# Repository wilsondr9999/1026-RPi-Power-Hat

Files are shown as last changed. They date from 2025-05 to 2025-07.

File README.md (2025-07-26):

## Introduction
This project is a HAT (hardware attached on top) for the Raspberry Pi, specifically designed for the RatRig V-Core4 3D printer.  This HAT adds some features to the printer that make the electronics wiring easier and more straightforward, and prevent certain problems that can occur with the original RatRig design.

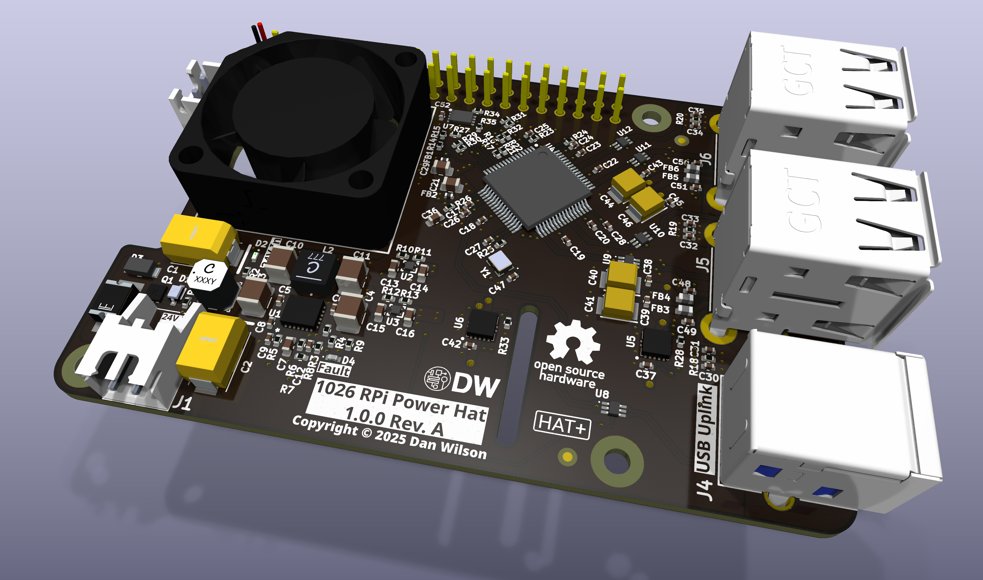
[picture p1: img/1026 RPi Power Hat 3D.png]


## Features
This HAT does the following:
- Removes the 5V power connection from the Octopus 3D printer control board that was used to power the Raspberry Pi, and replaces it with an on-board, high-current power regulator that can take 24V input directly.  This provides up to 20W (4A of 5V power) to the Raspberry Pi and all of its USB peripherals, rather than relying on the 5V regulator on the Octopus board.
- Provides an additional 4 USB ports to the Raspberry Pi using an on-board USB 2.0 hub IC.  This brings the total number of USB ports available for the 3D printer to 7 instead of 4.  The additional ports can support 2A of current each, with a total of 4A available to be shared among all 7 ports.  The USB hub IC used in this project is the Texas Instruments TUSB8041, a high-quality USB 2.0 hub.
- Includes a small fan that cools the CPU on the Raspberry Pi.  The out-of-the-box design of the V-Core4 has a large fan to cool the entire electronics enclosure, but by default it only runs when the 3D printer's stepper motors are energized.  When they are not, it does not run, and this can cause the Raspberry Pi's temperature to increase into the 60C+ range.  The on-board fan will keep the Pi below 45C when the stepper motors are not running.

## Fabrication
You can have the PCB made at any PCB manufacturer.  The Gerber files are already prepared in the Fabrication Exports folders.  One of the files is [1026 RPi Power Hat](KiCAD%20Project/Fabrication%20Exports%20-%20Oshpark/1026%20RPi%20Power%20Hat.zip) ready for upload to[ Oshpark](https://www.oshpark.com).  The other is [1026 RPi Power Hat](KiCAD%20Project/Fabrication%20Exports%20-%20PCBway/1026%20RPi%20Power%20Hat.kicad_pcb_gerber.zip) ready for upload to [PCBway](https://www.pcbway.com).  If you want to modify the design, the KiCAD project is available in the KiCAD folder.  The PCB is a 4-layer design, your PCB manufacturer needs to support a minimum trace/space of 5 mil (0.127 mm).

For assembly, the recommended method is to use solder paste and a stencil with a reflow oven or hot air station.  The stencil can be made from the [1026 RPi Power Hat-F_Paste](KiCAD%20Project/Fabrication%20Exports/1026%20RPi%20Power%20Hat-F_Paste.gbr) file in the Fabrication Exports folder.  Inexpensive stencils are available from [OshStencils](https://www.oshstencils.com/#).

## Bill of Materials (BOM)
The bill of materials to assemble this project is available in the file [1026 RPi Power Hat](KiCAD%20Project/BOM/1026%20RPi%20Power%20Hat.csv).  Almost all electronic parts are available from Mouser or Digikey.  One exception is the two inductors (L1, L2), these are probably easiest to purchase directly from CoilCraft, the link is in the BOM file.  Some miscellaneous hardware can be purchased from Amazon, those links are also in the BOM file.

## Assembly - Spreading Solder Paste for Reflow
To assemble the unit yourself, you will need a stencil and solder paste, along with a reflow oven or hot air station.  You can obtain the stencil as described above int the Fabrication section.

There is a solder stencil jig that can be 3D printed in the FreeCAD Project folder.  The file [1026 RPi Power Hat SSJ](FreeCAD%20Project/Solder%20Stencil%20Jig%20V2/1026%20RPi%20Power%20Hat%20SSJ.stl) (STL) can be imported into your preferred slicer and printed with the following settings:

- 0.2 mm layer height
- 0.4 mm nozzle
- 15% infill, use the Gyroid pattern
- PLA material

If you use PrusaSlicer, the file [1026 RPi Power Hat SSJ](FreeCAD%20Project/Solder%20Stencil%20Jig%20V2/1026%20RPi%20Power%20Hat%20SSJ.3mf) (3MF) already has these settings.  You may need to adjust the print speeds for your printer, the speeds in the 3MF file are set for a RatRig V-Minion and are quite fast.

If you want to change aspects of the Solder Stencil Jig, the FreeCAD file is available named [Solder Stencil Jig V2](FreeCAD%20Project/Solder%20Stencil%20Jig%20V2/Solder%20Stencil%20Jig%20V2.FCStd), it is a parametric file that can generate a solder stencil jig for any PCB.

Once you have obtained the manufactured PCB, the stencil, and have printed the solder stencil jig, you should have all 3 of them as such:

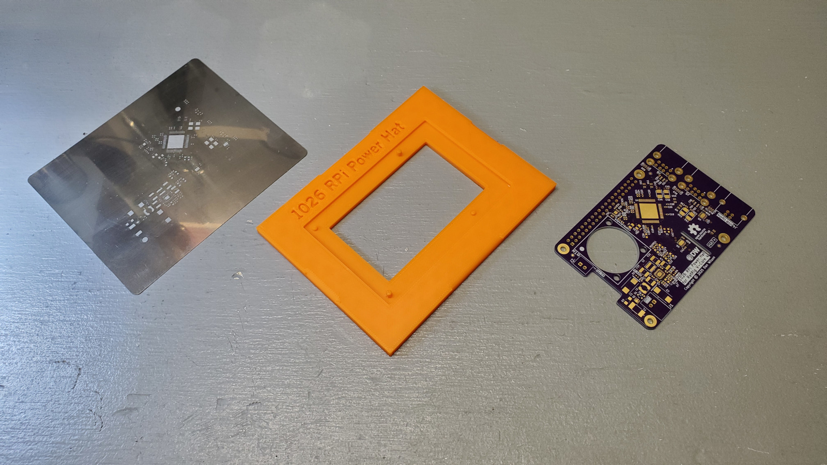
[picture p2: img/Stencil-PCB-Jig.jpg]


Insert the PCB into the solder stencil jig, the registration pins will go through the mounting holes:

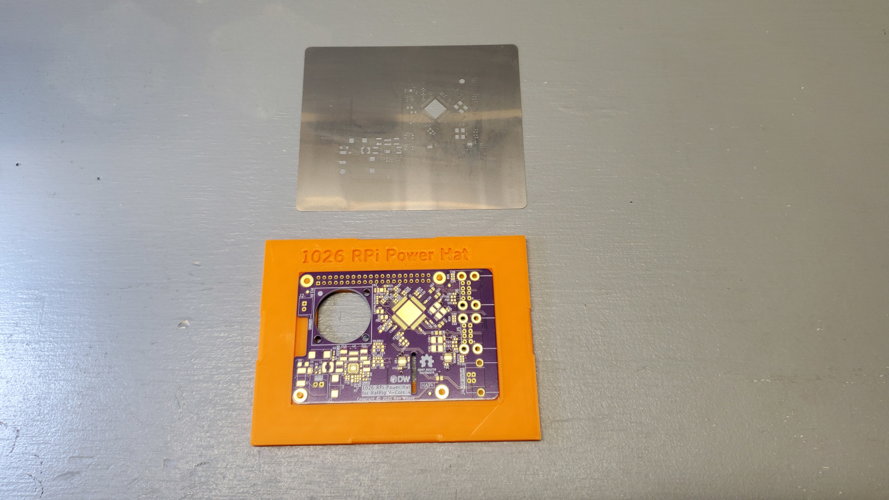
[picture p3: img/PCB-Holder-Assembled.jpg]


Clean the PCB surface with isopropyl alcohol (99%), and clean the stencil the same way.  The PCB should look completely clean under a microscope, with no dust, hair, fibers, or oils on the PCB:

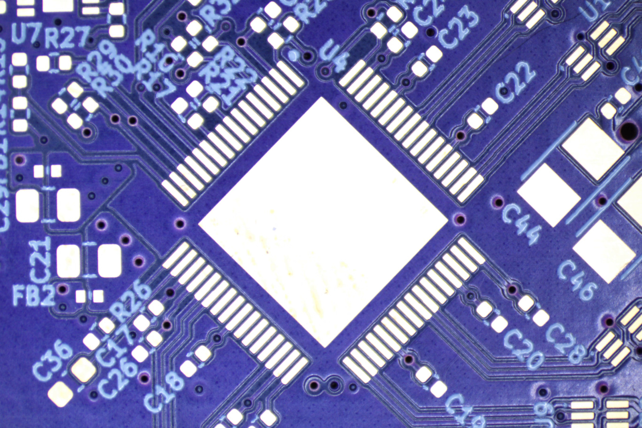
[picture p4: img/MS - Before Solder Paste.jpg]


Finally, place the stencil on top of the jig, two of the registration pins go through the stencil to align it:

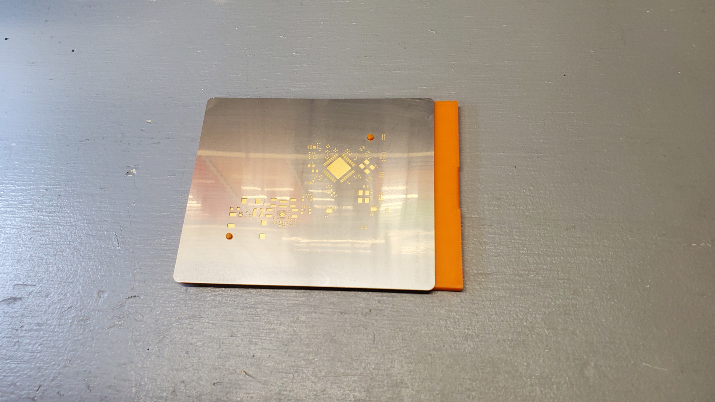
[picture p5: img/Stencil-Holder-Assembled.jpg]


Spread the solder paste onto the stencil using a paste spreader or old plastic card.  Ensure the solder paste fills all openings in the stencil.  Remove the stencil, then carefully pop out the PCB from the jig.  **Do NOT leave the PCB in the jig while placing the components in the next step!**  The components will dislodge from the PCB when you pop it out later.

Your PCB pads should look like this after solder paste is applied:

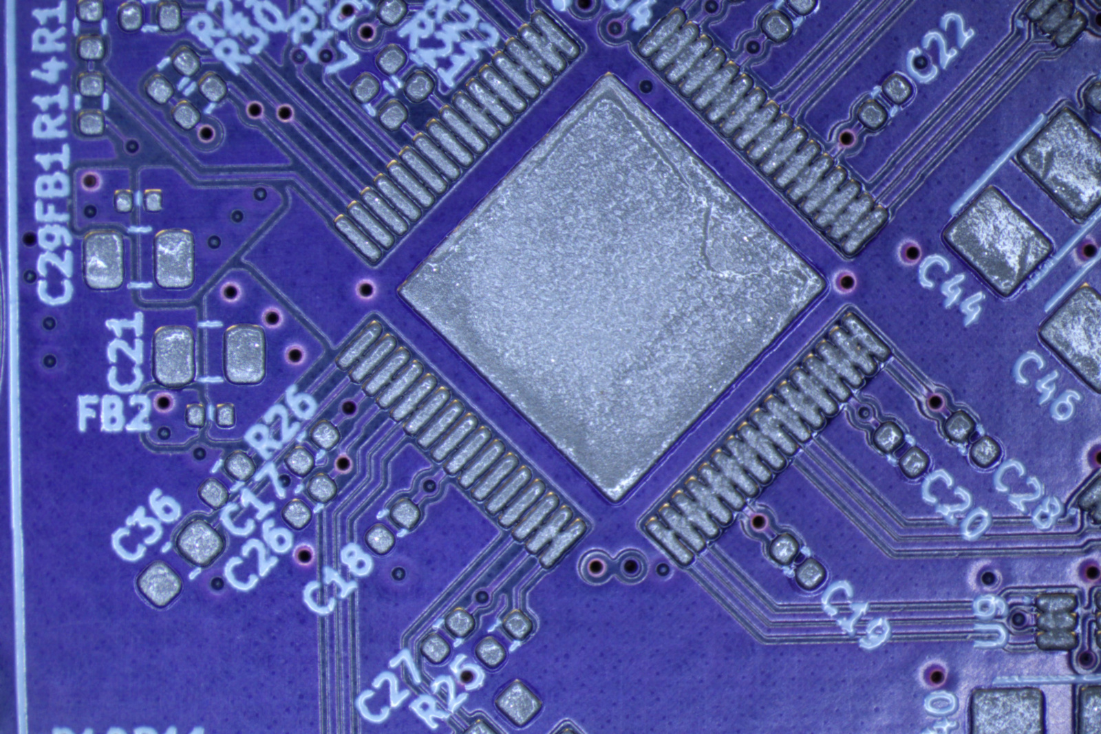
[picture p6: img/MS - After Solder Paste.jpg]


## Assembly - Placing Components
Begin placing the surface mount components onto the PCB.  Start with the smallest components (0402 surface mount passives -- resistors, capacitors), and work up to the larger components.  Do not place any through-hole components at this stage.  You can place the components with tweezers or use an air-pick tool if available.

You do not need to perfectly align every component, if the component leads are touching the solder paste on the correct pads and the component is flat, you're fine.  When the board is reflowed, the surface tension of the solder paste will pull the components into very good alignment with the pads.

If the solder paste has expanded and is touching adjacent pads like on the USB chip, it probably will not cause an issue.  When the solder melts, the flux and the solder mask on the PCB will direct the liquid solder to the pad and separate the adjacent pins.  After reflow, check carefully for any solder bridges that may remain.

Double- and Triple- check the polarity of the diodes, LEDs, and capacitors when you place them on the PCB, and check the pin 1 marker of all of the chips.  The silkscreen markings on the PCB match the mark on the component (provided you are using the exact component listed in the BOM).

The 0402 LEDs in particular are very difficult to identify which end is the cathode, so carefully check.

Unlike aluminum electrolytic capacitors where the negative terminal is marked, the tantalum polymer capacitors you will be soldering here have the positive terminal marked.  This matches the silkscreen on the PCB.

Once you get to the larger components, you need to carefully look at the pin alignment, especially on the big USB chip.  It is very easy to misalign the chip by one pin in any direction, so double-check it.

Your PCB should look like this after the components are placed:

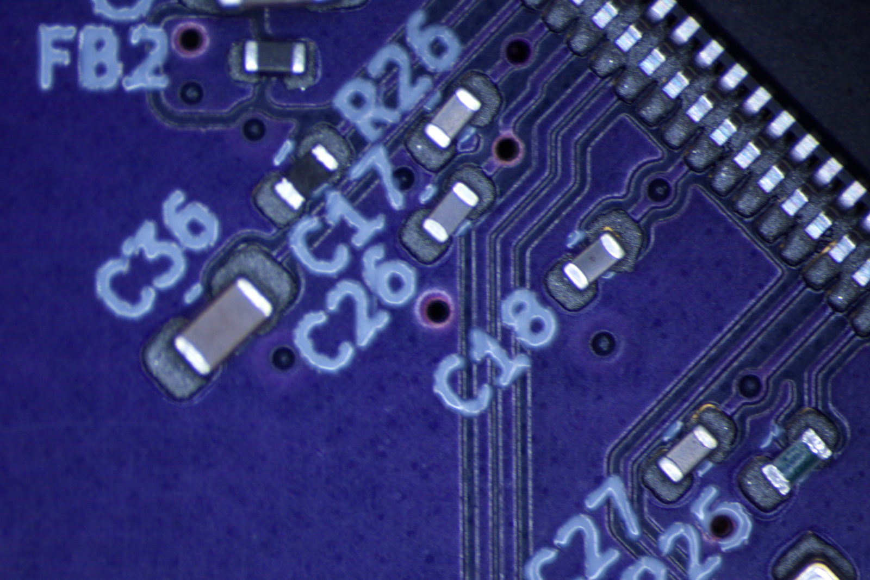
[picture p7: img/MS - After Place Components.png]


## Assembly - Reflow
Reflow the PCB in a reflow oven using the solder paste manufacturer's recommended reflow profile.

If you are going to reflow with a hot air station, you need to be extremely careful with the heat level, as some components like the LEDs can melt if the temperature is too high.  Furthermore, the air flow needs to be low, as some of the very small 0402 components can be blown off the PCB.  If you have a PCB preheater, it will be very helpful here.

## Assembly - Through-Hole Components
Solder the through-hole components onto the PCB in the following order:
The following components are on the TOP side of the PCB, so we solder them on from the back side (bottom):
- 2x JST-XH-2 connectors for input power and the fan.  The fan connector is a top-entry, the input power connector is a side-entry.
- 1x USB-B connector for uplink
- 2x USB-A (2 port) connectors for downlink

The following component is on the BOTTOM side of the PCB, so we solder it on from the front side (top):
- 2x20 pin header

Look at the silkscreen marks on the PCB, they identify the side where the component goes.  Then you solder from the other side.

## Cleaning
It is recommended to clean the PCB after soldering to remove all remaining flux.  Isopropyl alcohol will remove it, but may require light brushing with a toothbrush, and may require multiple passes to remove all of the flux.  Use only distilled water or isopropyl alcohol as solvents for cleaning the PCB.  An ultrasonic cleaner with a detergent also works well if available, but **never use Isopropyl alcohol in an ultrasonic cleaner, use distilled water and detergent only.**

If you have used distilled water for rinsing or in an ultrasonic cleaner, dry the PCB using compressed air, and then further dry it in an oven at 125C for 2 hours.

Once you're finished, your PCB should look like this:

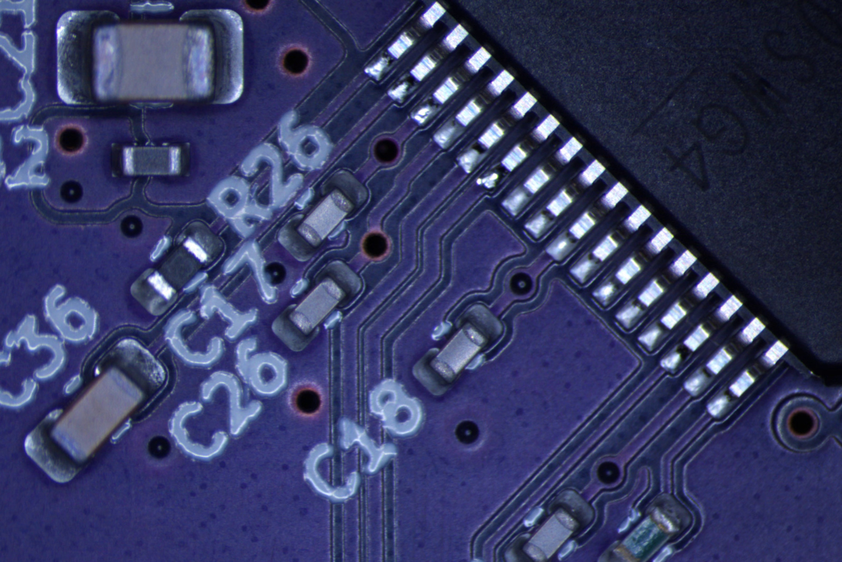
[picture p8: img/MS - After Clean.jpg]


## Fan Preparation
The fan that is to be installed on the PCB needs to have the JST-XH-2 connector (part number XHP-2) installed.  Cut the wires on the fan to a length of approximately 2 inches (5 cm), then crimp on two of the JST contacts (part number SXH-001T-P0.6).  Insert the crimped wire/contacts into the XHP-2 connector, pay attention to the required polarity.  The polarity is marked on the PCB, the fan's red wire goes to the positive (+) terminal on the PCB, this is the terminal closest to the M2.5 mounting screw hole.

Use the following picture as a reference for the fan wiring:

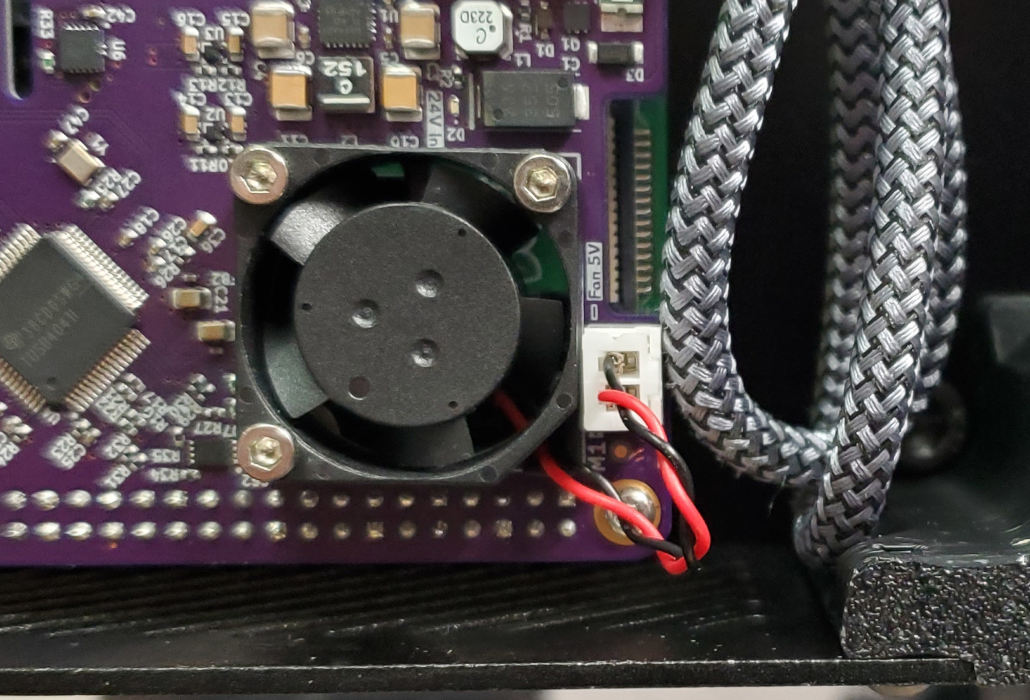
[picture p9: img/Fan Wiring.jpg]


Once the fan is terminated, attach it to the PCB using 3x M2.5 16mm hex cap screws and 3 M2.5 hex nuts on the underside of the PCB.  Ensure the fan is oriented correctly such that the air flow is from the top of the PCB through to the bottom of the PCB.  This will blow air onto the Raspberry Pi's CPU that is below.  For maximum effectiveness, add a passive heat sink to the Raspberry Pi's CPU chip.  There are two arrows on the side of the fan that show you both the rotation direction as well as the air flow direction, you can use these to assist you in orienting the fan in the correct position.

## 5V Regulator Heat Sink
There is a square on the bottom side of the PCB that is 6mm x 6mm in size that is bare copper, not covered by solder mask.  This square is directly underneath the 5V regulator and needs to have a small copper heat sink attached to make sure the regulator stays cool.  The heat sink is listed in the BOM .csv file, and is available from Amazon.  Peel off the protective film on the heat sink and press it to the copper square so that it sticks on.  The fan's air flow will also help cool this heat sink.

## Installation into the RatRig V-Core 4
Prepare a 2-wire power lead to go from the 24V power supply in the V-Core4 to the power HAT.  Terminate the ends of the lead on the 24V power supply side using connectors applicable to your power supply.

Terminate the HAT ends of the leads using a JST-XH-2 connector (part number XHP-2) the same way you did the fan.  Crimp on two of the JST contacts (part number SXH-001T-P0.6).  Insert the crimped wire/contacts into the XHP-2 connector, pay attention to the required polarity.  The polarity is marked on the PCB, the negative lead is on the side of the PCB's JST-XH-2 connector that is closest to the M2.5 mounting screw hole.

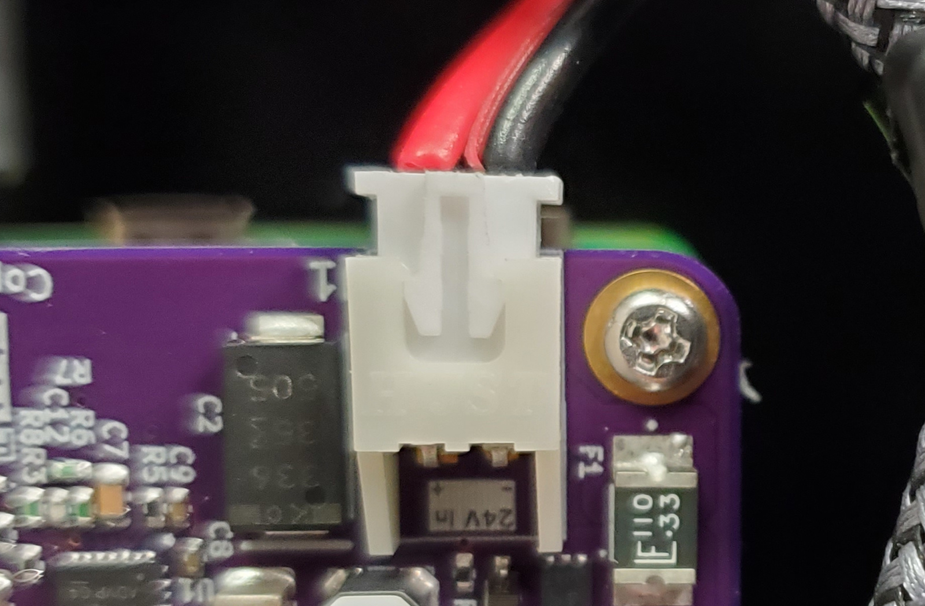
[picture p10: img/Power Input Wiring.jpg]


You will be assembling the HAT onto the top of your Raspberry Pi using 4 brass PCB standoffs (20mm length of the standoff + a 6 mm length of M2.5 threads) and 4 M2.5 x 6mm screws (pan-head phillips).  The BOM .csv file has an Amazon link to a kit that contains these parts.  Use the following photo to see how the HAT is supposed to be mounted on top of the Raspberry Pi:

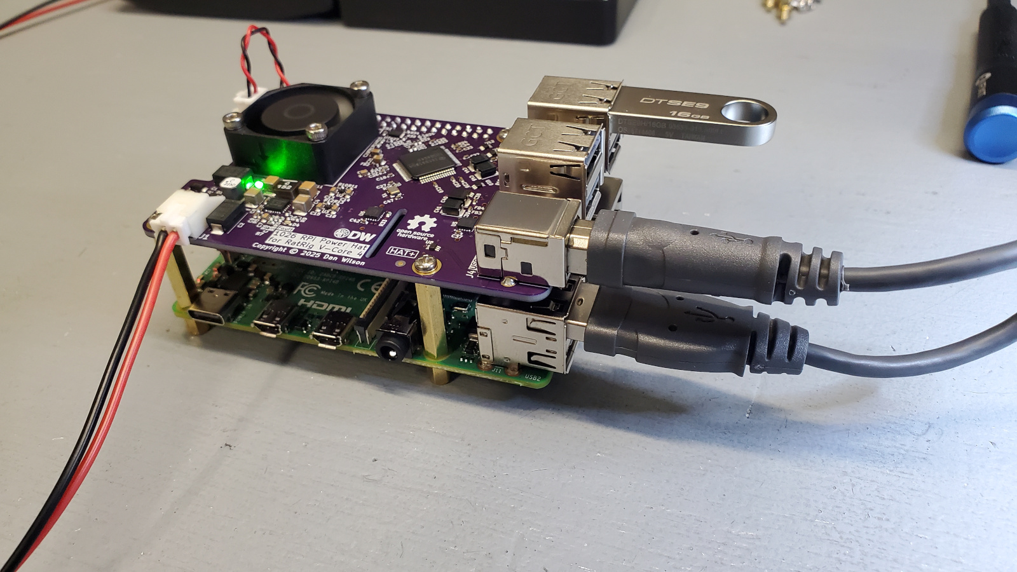
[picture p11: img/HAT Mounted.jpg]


Mount the HAT to the Raspberry Pi inside the V-Core4's electronics case.  The final result should look like this:

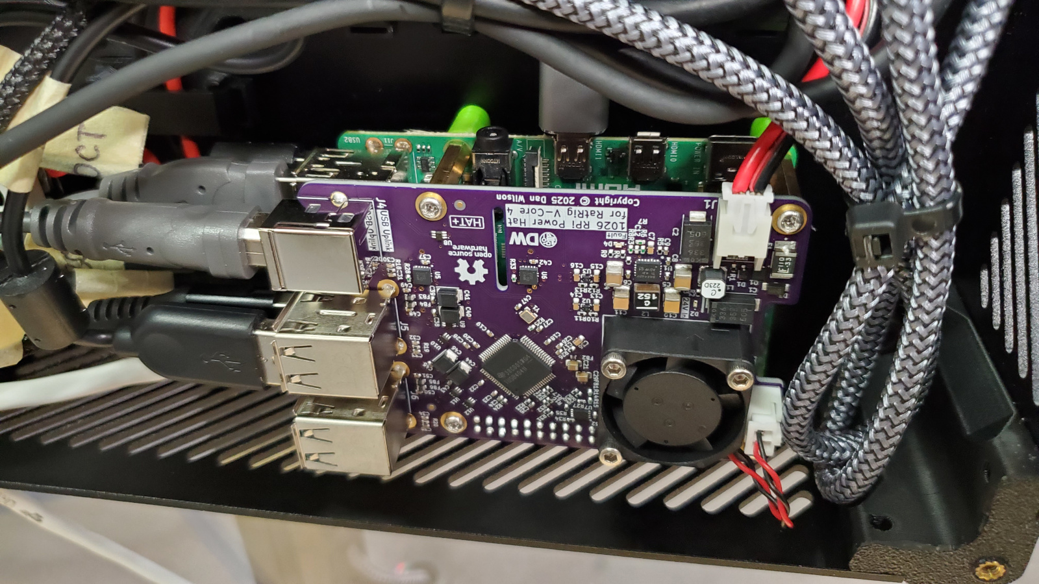
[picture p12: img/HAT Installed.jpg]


## USB Port Recommendations
Some of the USB devices on the RatRig V-Core4 have higher bandwidth requirements, and/or are more sensitive to issues than others.  Please use the following recommendations for which devices to plug where:

For all V-Core 4 models:
- Plug the USB-A to USB-B cable that connects the Raspberry Pi to the HAT using:
	- 1 USB-A 2.0 port on the Raspberry Pi (black plastic)
	- The USB-B port on the HAT

For CoreXY and Hybrid models:
- Toolhead / EBB42 board: Use a Raspberry Pi 3.0 (blue plastic) port
- Beacon Probe: Use a Raspberry Pi 3.0 (blue plastic) port
- Octopus Board: Use a Raspberry Pi 2.0 (black plastic) port
- Additional accessories, such as a chamber camera, nozzle camera, or touchscreen: Use a USB 2.0 port (black plastic) on the HAT

For IDEX models:
- Toolhead / EBB42 board 0: Use a Raspberry Pi 3.0 (blue plastic) port
- Toolhead / EBB42 board 1: Use the other Raspberry Pi 3.0 (blue plastic) port
- Beacon Probe: Use a Raspberry Pi 2.0 (black plastic) port
- Octopus Board: Use a USB 2.0 (black plastic) port on the HAT
- VAOC Offset Camera: Use a USB 2.0 (black plastic) port on the HAT
- Additional accessories, such as a chamber camera, nozzle camera, or touchscreen: Use a USB 2.0 port (black plastic) on the HAT

Your final installation should look like this:

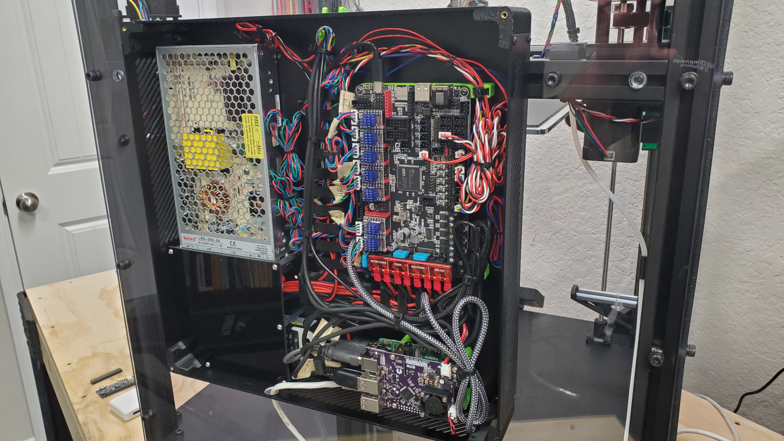
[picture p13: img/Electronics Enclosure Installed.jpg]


## Initial Power-Up
At this point, if everything is connected, you can power on the V-Core4.  The HAT will provide the 5V power to the Pi through the GPIO header.  You should see the green power-on LED lit on the HAT.  If you see the red Fault LED lit up on the HAT, check your input voltage, it must be above 22V for the HAT to power on.  If the voltage checks out OK but you still get a fault LED, this may indicate that you have a short on the HAT PCB.  Re-check all soldered connections.

The fault LED can also indicate an overcurrent condition (more than 20W / 4A used by the Pi + fan + all USB devices).  This should be unlikely, but is something to check.  Remove USB devices one at a time, starting with the accessories that are not part of the RatRig V-Core4 systems and see if the fault light goes out.

## Preparing the HAT in Linux
This HAT conforms to the Raspberry Pi HAT+ specification.  The HAT+ specification requires that the HAT contain an EEPROM with information that tells the Raspberry Pi what the HAT is and its capabilities.  We will program this EEPROM and set up the Raspberry PI to recognize it in the next steps.

### Establish a Command Session to your Raspberry Pi
Using an SSH client like [Putty](https://www.putty.org/), connect to your Raspberry Pi using it's IP address on port 22.  The default username and password for the Raspberry Pi, if you have prepared it using RatRig's instructions, is "pi" and "raspberry".  If you have changed these, use your own username and password that you have established.

Once in the command terminal, execute the following commands to prepare the EEPROM:

```
sudo -i
```

The above command will again ask you for the password, the default is "raspberry".

```
apt install cmake
cd /root
git clone https://github.com/raspberrypi/utils.git
cd utils/eeptools
cmake .
make
make install
wget https://github.com/wilsondr9999/1026-RPi-Power-Hat/blob/master/Extras/Linux%20EEPROM%20Preparation/myhat.eep
wget https://github.com/wilsondr9999/1026-RPi-Power-Hat/blob/master/Extras/Linux%20EEPROM%20Preparation/rr-vcore4-powerhat.dtbo
apt install i2c-tools
dtoverlay i2c-gpio i2c_gpio_sda=0 i2c_gpio_scl=1 bus=9
i2cdetect -y 9
```

 The final command above should show you a matrix of detected I2C addresses on the GPIO header.  The HAT is supposed to be detected on address 53, and the number 53 should show up in the matrix.  If it does not, check the HAT for soldering problems.  If it does, proceed with flashing the EEPROM:

```
./eepflash.sh -w -t=24c32 -d=9 -a=53 -f=myhat.eep
```

Make sure the above command completes successfully and does not issue an error message.

```
cp rr-vcore4-powerhat.dtbo /boot/overlays/
sh -c "echo rr-vcore4-powerhat.dtbo >> /boot/config.txt"
```

Now we can reboot the Pi:

```
reboot
```

Once the Pi is rebooted, you can verify that the USB hub is detected and functioning.  Connect to a command session again using your SSH client, and issue the following command:

```
lsusb
```

In the device listing, you should see the HAT's USB hub:

```
Bus 001 Device 005: ID 0451:8142 Texas Instruments, Inc. TUSB8041 4-Port Hub
```

You should also be able to see the RatRig printer devices connected:

```
Bus 001 Device 006: ID 1d50:614e OpenMoko, Inc. stm32f446xx
Bus 001 Device 004: ID 04d8:e72b Microchip Technology, Inc. Beacon RevH
Bus 001 Device 003: ID 1d50:614e OpenMoko, Inc. stm32g0b1xx
Bus 001 Device 002: ID 2109:3431 VIA Labs, Inc. Hub
```

You should also see any additional accessory devices you have added, for example:

```
Bus 001 Device 008: ID 04d9:8030 Holtek Semiconductor, Inc. BTT-HDMI7
Bus 001 Device 007: ID 046d:0825 Logitech, Inc. Webcam C270
```

## Licensing
This project is licensed under two separate licenses:

The hardware design is licensed under the CERN Open Hardware License Version 2 - Weakly Reciprocal.  This copyleft license requires that if you use this device in your product or redistribute this device or its derivatives in any way, that you must:

- Provide the end-users with this license and copyright notice.
- State any changes you have made to the original device, its files, or its documentation.
- Publish your modifications of the device, its files, and its documentation under the same license.
- Indicate to the end-user the original source (this GitHub archive) and that your work is a derivative and/or redistribution.
- The license is "weakly reciprocal" in that it only requires these actions for the modified device itself, not the entire end product that you have incorporated it into.  The rest of the product does not have to follow this license and is not affected by this license.

The documentation, images, and instructions are licensed under the Creative Commons Attribution-ShareAlike 4.0 International Public License.  This copyleft license requires that if you use this device in your product or redistribute this device or its derivatives in any way, that you must:

- Provide the end-users with this license and copyright notice.
- State any changes you have made to the original device, its files, or its documentation.
- Publish your modifications of the device, its files, and its documentation under the same license.
- Indicate to the end-user the original source (this GitHub archive) and that your work is a derivative and/or redistribution.

As stated by the licenses, all uses of this project require attribution and require open-source release under the same licenses.

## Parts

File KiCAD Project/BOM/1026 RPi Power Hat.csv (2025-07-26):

Reference | Qty | Value | DNP | Exclude from BOM | Footprint | Datasheet | Height | Manufacturer_Name | Manufacturer_Part_Number | Mouser Part Number | Product Page | Spec | Description
C1,C2 | 2 | T521D336M035ATE065 |  |  | DW_Passives:[C] Kemet Tantalum Polymer T521X | https://www.mouser.com/datasheet/2/447/KEM_T2076_T52X_530-3317002.pdf | 4.3 | KEMET | T521D336M035ATE065 | 80-T521D336M35ATE65 | https://www.mouser.com/ProductDetail/KEMET/T521D336M035ATE065?qs=1gHfTFoodzaHxXmfIl2UDw%3D%3D | 33u 35V | Input Filter Cap Tant Poly
C3,C4 | 2 | GRJ32ER71H106KE11K |  |  | Capacitor_SMD:C_1210_3225Metric | https://www.mouser.com/datasheet/2/281/1/GRJ32ER71H106KE11_02A-3155002.pdf | 2.8 | Murata | GRJ32ER71H106KE11K | 81-GRJ32ER71H106KE1K | https://www.mouser.com/ProductDetail/Murata-Electronics/GRJ32ER71H106KE11K?qs=lEfY3O89Aqkc0aIiWmlJZw%3D%3D | 10u 50V | Input Capacitor
C5,C6 | 2 | GCM155R71H223KA55D |  |  | Capacitor_SMD:C_0402_1005Metric | https://www.mouser.com/datasheet/2/281/1/GCM155R71H223KA55_01A-3142318.pdf | 0.55 | Murata | GCM155R71H223KA55D | 81-GCM155R71H223KA5D | https://www.mouser.com/ProductDetail/Murata-Electronics/GCM155R71H223KA55D?qs=aEuGZpxfbxWRPp0xzcGE2w%3D%3D | 22n 50V | Input Capacitor
C7,C13,C14,C15,C16,C36 | 6 | GCM188R71C105KA64J |  |  | Capacitor_SMD:C_0603_1608Metric | https://www.mouser.com/datasheet/2/281/1/GCM188R71C105KA64_04A-3143889.pdf | 0.9 | Murata | GCM188R71C105KA64J | 81-GCM188R71C105KA4J | https://www.mouser.com/ProductDetail/Murata-Electronics/GCM188R71C105KA64J?qs=4%252BGqC78dy0BN5WaW5TLgXw%3D%3D | 1u 16V | Vcc Capacitor
C8,C9,C17,C18,C19,C20,C22,C23,C24,C25,C26,C27,C28,C37,C38,C39,C42,C43,C45,C47,C48,C49,C50,C51,C52 | 25 | GCM155R71C104KA55D |  |  | Capacitor_SMD:C_0402_1005Metric | https://www.mouser.com/datasheet/2/281/1/GCM155R71C104KA55_01A-3142292.pdf | 0.55 | Murata | GCM155R71C104KA55D | 81-GCM155R71C104KA5D | https://www.mouser.com/ProductDetail/Murata-Electronics/GCM155R71C104KA55D?qs=aEuGZpxfbxVTPYRtXT4ecg%3D%3D | 100n 16V | Cboot Capacitor
C10,C11 | 2 | GCM32ER71C226ME19L |  |  | Capacitor_SMD:C_1210_3225Metric | https://www.mouser.com/datasheet/2/281/1/GCM32ER71C226ME19_01A-3146418.pdf | 2.7 | Murata | GCM32ER71C226ME19L | 81-GCM32ER71C226ME9L | https://www.mouser.com/ProductDetail/Murata-Electronics/GCM32ER71C226ME19L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 | 22u 16V | Output Capacitor
C12 | 1 | VJ0402A100GXJCW1BC |  |  | Capacitor_SMD:C_0402_1005Metric | https://www.vishay.com/doc?28548 | 0.5 | Vishay | VJ0402A100GXJCW1BC | 77-VJ0402A100GXJCBC | https://www.mouser.com/ProductDetail/77-VJ0402A100GXJCBC | 10p 16V C0G | Cff Capacitor
C21,C29 | 2 | GCM21BR70J106KE22K |  |  | Capacitor_SMD:C_0805_2012Metric | https://www.mouser.com/datasheet/2/281/1/GCM21BR70J106KE22_01A-3145361.pdf | 1.4 | Murata | GCM21BR70J106KE22K | 81-GCM21BR70J106KE2K | https://www.mouser.com/ProductDetail/Murata-Electronics/GCM21BR70J106KE22K | 10u 6V3 | 3V3 Bus Capacitor
C30,C33,C35 | 3 | GCM155R71H104KE02J |  |  | Capacitor_SMD:C_0402_1005Metric | https://www.mouser.com/datasheet/2/281/1/GCM155R71H104KE02_01A-3142168.pdf | 0.55 | Murata | GCM155R71H104KE02J | 81-GCM155R71H104KE2J | https://www.mouser.com/ProductDetail/Murata-Electronics/GCM155R71C104KA55D?qs=aEuGZpxfbxVTPYRtXT4ecg%3D%3D | 100n 50V | USB Shield EMI Cap
C31,C32,C34 | 3 | GCM155R71H102KA37D |  |  | Capacitor_SMD:C_0402_1005Metric | https://www.mouser.com/datasheet/2/281/1/GCM155R71H102KA37_01A-3142409.pdf | 0.55 | Murata | GCM155R71H102KA37D | 81-GCM155R71H102KA7D | https://www.mouser.com/ProductDetail/Murata-Electronics/GCM155R71H102KA37D | 1n 50V | USB Shield EMI Cap
C40,C41,C44,C46 | 4 | TCJB157M006R0070 |  |  | DW_Passives:[C] Kyocera AVC Tant Poly TCJB157M006R0070 | https://www.mouser.com/datasheet/2/40/TCJ-2887130.pdf | 2.1 | Kyocera AVX | TCJB157M006R0070 | 581-TCJB157M006R0070 | https://www.mouser.com/ProductDetail/KYOCERA-AVX/TCJB157M006R0070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 | 150u 6V3 | AVX 150uF SMD Solid Polymer Tantalum Electrolytic Capacitor, 6.3 V dc +/-20%, TCJ Series
D1 | 1 | PDZ10B,115 |  |  | DW_Semiconductors:[D] Nexperia Zener PDZ10B,115 10V | https://www.mouser.com/datasheet/2/916/PDZ_B_SER-1548405.pdf | 1.1 | Nexperia | PDZ10B,115 | 771-PDZ10B115 | https://www.mouser.com/ProductDetail/Nexperia/PDZ10B115?qs=LOCUfHb8d9t6BsAtogB8tA%3D%3D | 10V 2% 400mW | Rev Power Prot Diode
D2 | 1 | 150040GS73220 |  |  | DW_Optoelectronics:[D] Wurth Elektronik 150040GS73220 | https://www.we-online.com/components/products/datasheet/150040GS73220.pdf | 0.35 | Wurth Elektronik | 150040GS73220 | 710-150040GS73220 | https://www.mouser.com/ProductDetail/Wurth-Elektronik/150040GS73220?qs=u16ybLDytRZ9vktXLUK1Kg%3D%3D | 0603 525nm | Input Power LED
D3 | 1 | SMF24CA |  |  | DW_CircuitProtection:[D] Littelfuse SMF24CA 24V 200W | https://www.mouser.com/datasheet/2/240/media-3321418.pdf | 1.08 | Littelfuse | SMF24CA | 576-SMF24CA | https://www.mouser.com/ProductDetail/Littelfuse/SMF24CA?qs=d0WKAl%252BL4KZ7Y3Ls3uQ%252BqA%3D%3D | TVS BiDir 24V 200W | Input TVS Surge Suppression
D4 | 1 | 150040RS73240 |  |  | DW_Optoelectronics:[D] Wurth Elektronik 150040RS73240 | https://katalog.we-online.de/pbs/datasheet/150040RS73240.pdf | 0.5 | Wurth Elektronik | 150040RS73240 | 710-150040RS73240 | https://www.mouser.co.uk/ProductDetail/Wurth-Elektronik/150040RS73240?qs=8Aam6%252B7C6HGMiInmnlrBiw%3D%3D | 0402 630nm | Fault LED
F1 | 1 | 1812L110/33MR |  |  | DW_CircuitProtection:[F] Littelfuse PPTC 1812L110/33MR | https://www.littelfuse.com/assetdocs/resettable-ptcs-1812l-datasheet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 | 1.25 | LITTELFUSE | 1812L110/33MR | 576-1812L110/33MR | https://www.mouser.com/ProductDetail/Littelfuse/1812L110-33MR?qs=PWhpLWeW8wdL8%252Bas2HFkoA%3D%3D | 1.1A 33V | Input PPTC Resettable Fuse
FB1,FB2 | 2 | BLM15PX221SZ1D |  |  | DW_Passives:[FB] Murata BLM15PX221SZ1D | https://www.mouser.com/datasheet/2/281/QNFA9118-1915745.pdf | 0.55 | Murata Electronics | BLM15PX221SZ1D | 81-BLM15PX221SZ1D | https://www.mouser.com/ProductDetail/Murata-Electronics/BLM15PX221SZ1D | 220 ohm 100MHz | BLM15_Z1D Series EMI Suppression Filter 220+/-25% at 100MHz 1.4A @85
FB3,FB4,FB5,FB6 | 4 | BLM18KG221SN1D |  |  | DW_Passives:[FB] Murata BLM18KG221SN1D 220ohm 2.2A | https://www.mouser.com/datasheet/2/281/ENFA0003-1915778.pdf | 0.55 | Murata Electronics | BLM18KG221SN1D | 81-BLM18KG221SN1D | https://www.mouser.com/ProductDetail/Murata-Electronics/BLM18KG221SN1D | 220ohm 2.2A | BLM18 Series EMI Suppression Filter 220+/-25% at 100MHz 2.2A @85
J1 | 1 | S2B-XH-A-1 |  |  | DW_Connectors:[J] JST S2B-XH-A-1 | https://www.jst-mfg.com/product/pdf/eng/eXH.pdf | 7 mm | JST | S2B-XH-A-1 | 306-S2BXHA1LFSN | https://www.mouser.com/ProductDetail/JST-Commercial/S2B-XH-A-1LFSN?qs=QpmGXVUTftHhNeC%252BPQWeTw%3D%3D | JST-XH-2 Side | Input Power Connector
J2 | 1 | B2B-XH-A(LF)(SN) |  |  | DW_Connectors:JST_B2B-XH-A(LF)(SN) | https://www.jst-mfg.com/product/pdf/eng/eXH.pdf | 7 mm | JST | B2B-XH-A(LF)(SN) | 306-B2BXHALFSNP | https://www.mouser.com/ProductDetail/JST-Commercial/B2B-XH-ALFSN?qs=cdbOS8ANM9DdcSn9qRmfCw%3D%3D | JST-XH-2 | Connector Header Through Hole 2 position 0.098 (2.50mm)
J3 | 1 | ESW-120-34-G-D |  |  | DW_Connectors:[J] Samtec Elevated Socket Strip ESW-120-34-G-D | https://www.mouser.com/datasheet/2/527/esw_th-2854089.pdf | 16.13 | Samtec | ESW-120-34-G-D | 200-ESW12034GD | https://www.mouser.com/ProductDetail/Samtec/ESW-120-34-G-D?qs=0lQeLiL1qyZhSkNUS%2FXSIA%3D%3D | 20x2 0.28" Header | Elevated Socket Strip 0.28in 20x2 16.13mmH Gold
J4 | 1 | USB1030-GF-P-B-B |  |  | DW_Connectors:[J] GCT USB-B 2.0 Connector PCB USB1030-GF-P-B-B | https://www.mouser.com/datasheet/2/837/USB1030-1948845.pdf | 10.95 | GCT | USB1030-GF-P-B-B | 640-USB1030-GF-P-B-B | https://www.mouser.com/ProductDetail/GCT/USB1030-GF-P-B-B?qs=KUoIvG%2F9Ila4yhPpaOZhHA%3D%3D | USB Connectors USB B Skt, TH, GF, USB-B 2.0 | USB Connectors USB B Skt, TH, GF, USB-B 2.0
J5,J6 | 2 | USB1035-GF-P-0-B-B |  |  | DW_Connectors:[J] GCT USB-A x2 2.0 Connector USB1035-GF-P-0-B-B | https://www.mouser.com/datasheet/2/837/USB1035-1948815.pdf | 15.32 | GCT | USB1035-GF-P-0-B-B | 640-USB1035GFP0BB | https://www.mouser.com/ProductDetail/GCT/USB1035-GF-P-0-B-B?qs=KUoIvG%2F9IlZdvtWwZEQX0g%3D%3D | USB Connectors USB A Skt, TH, GF, USB-A 2.0 | USB-A (USB TYPE-A), Stacked USB 2.0 Receptacle Connector 8 Position Through Hole, Right Angle
L1 | 1 | LPS4040-223 |  |  | DW_Passives:[L] Coilcraft Inductor LPS4040 | https://www.coilcraft.com/getmedia/f7e40242-0039-4f27-a16a-aab00a43fe02/lps4040.pdf | 4 | Coilcraft | LPS4040-223 |  | https://www.coilcraft.com/en-us/products/power/shielded-inductors/ferrite-drum/lps/lps4040/lps4040-223/ | 22uH 0.8A 210mohm | Input Filter Inductor
L2 | 1 | XGL4025-152ME |  |  | DW_Passives:[L] Coilcraft Inductor XGL4025 | https://www.coilcraft.com/getmedia/68c6d53c-572d-430a-a300-0b846e02622d/xgl4025.pdf | 2.5 | Coilcraft | XGL4025-152ME |  | https://www.coilcraft.com/en-us/products/power/shielded-inductors/molded-inductor/xgl/xgl4025/?skuId=32087|32107 | 1.5u 8A 11mohm | SMPS Buck Inductor
M1 | 1 | CFM-2510B-070-140 |  |  | DW_Mechanical:[Fan] SameSky CFM-2510B-070-140 | https://www.sameskydevices.com/product/resource/cfm-25b.pdf | 10 | Same Sky | CFM-2510B-070-140 | 490-CFM2510B-070-140 | https://www.mouser.com/ProductDetail/Same-Sky/CFM-2510B-070-140?qs=GedFDFLaBXHD1VXBjs5CMA%3D%3D | 5V 7000RPM 25mm | DC Fans dc axial fan, 25 mm square, 10 mm, 5 Vdc, omniCOOL, 5000 RPM, 1.35 CFM
Q1 | 1 | BUK6D120-60PX |  |  | DW_Semiconductors:[Q] Nexperia BUK6D120-60PX P-Ch 60V 8A | https://www.mouser.com/datasheet/2/916/BUK6D120_60P-1539811.pdf | 0.65 | Nexperia | BUK6D120-60PX | 771-BUK6D120-60PX | https://www.mouser.com/ProductDetail/Nexperia/BUK6D120-60PX?qs=F5EMLAvA7IBtoNC2L3hOcQ%3D%3D | P-Ch 60V 8A | Rev Power Prot MOSFET
R1 | 1 | 15K |  |  | Resistor_SMD:R_0402_1005Metric | https://www.vishay.com/doc?20035 | 0.4 | Vishay | CRCW040215K0FKED | 71-CRCW0402-15K-E3 | https://www.mouser.com/ProductDetail/Vishay-Dale/CRCW040215K0FKED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 | 15K 63mW | Rev Power Prot Zener Resistor
R2 | 1 | 47K |  |  | Resistor_SMD:R_0402_1005Metric | https://www.vishay.com/docs/20035/dcrcwe3.pdf | 0.4 | Vishay | CRCW040247K0FKED | 71-CRCW0402-47K-E3 | https://www.mouser.com/ProductDetail/Vishay-Dale/CRCW040247K0FKED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 | 47K 63mW | Outut Power On LED Resistor
R3 | 1 | 95K3 |  |  | Resistor_SMD:R_0402_1005Metric | https://www.vishay.com/docs/28758/tnpw_e3.pdf | 0.4 | Vishay | CRCW040295K3FKED | 71-CRCW0402-95.3K-E3 | https://www.mouser.com/ProductDetail/Vishay-Dale/CRCW040295K3FKED?qs=lxmYmG9KtX%2FBpXlMXoZLjA%3D%3D | 95K3 63mW | UVLO Rtop
R4 | 1 | 6K34 |  |  | Resistor_SMD:R_0402_1005Metric | https://www.vishay.com/docs/28758/tnpw_e3.pdf | 0.4 | Vishay | CRCW04026K34FKEDC | 71-CRCW04026K34FKEDC | https://www.mouser.com/ProductDetail/Vishay-Dale/CRCW04026K34FKEDC?qs=E3Y5ESvWgWNSgvhw%252BFYhHA%3D%3D | 6K34 63mW | UVLO Rbot
R5 | 1 | 4R7 |  |  | Resistor_SMD:R_0402_1005Metric | https://www.vishay.com/docs/28758/tnpw_e3.pdf | 0.4 | Vishay | CRCW04024R70FNED | 71-CRCW04024R70FNED | https://www.mouser.com/ProductDetail/Vishay-Dale/CRCW04024R70FNED | 4R7 63mW | Bias Filter Resistor
R6 | 1 | 56K2 |  |  | Resistor_SMD:R_0402_1005Metric | https://www.vishay.com/doc?28758 | 0.4 | Vishay | TNPW040256K2BEED | 71-TNPW040256K2BEED | https://www.mouser.com/ProductDetail/Vishay-Dale/TNPW040256K2BEED?qs=wTZ%2FFzl837b3rYPo5yoVJg%3D%3D | 56K2 130mW | Rfbtop
R7 | 1 | 1K |  |  | Resistor_SMD:R_0402_1005Metric | https://www.vishay.com/doc?28758 | 0.4 | Vishay | TNPW04021K00BEED | 71-TNPW04021K00BEED | https://www.mouser.com/ProductDetail/Vishay-Dale/TNPW04021K00BEED | 1K 130mW | Rfbff
R8 | 1 | 13K7 |  |  | Resistor_SMD:R_0402_1005Metric | https://www.vishay.com/doc?28758 | 0.4 | Vishay | TNPW040213K7BEED | 71-TNPW040213K7BEED | https://www.mouser.com/ProductDetail/Vishay-Dale/TNPW040213K7BEED?qs=wTZ%2FFzl837aatGf%2Fvi%2Fe%252Bg%3D%3D | 13K7 130mW | Rfbbot
R9 | 1 | 7K5 |  |  | Resistor_SMD:R_0402_1005Metric | https://www.vishay.com/doc?20066 | 0.4 | Vishay | RCC04027K50FKED | 71-RCC04027K50FKED | https://www.mouser.com/ProductDetail/Vishay-Dale/RCC04027K50FKED?qs=VVKQmw408U%252BJEndTfkVZSA%3D%3D | 7K5 125mW | Fault LED Resistor
R10 | 1 | 12K7 |  |  | Resistor_SMD:R_0402_1005Metric | https://www.vishay.com/docs/28773/crcwce3.pdf | 0.35 | Vishay | CRCW040212K7FKED | 71-CRCW0402-12.7K-E3 | https://www.mouser.com/ProductDetail/Vishay-Dale/CRCW040212K7FKED | 12K7 63mW | 1V1 UVLO Rt
R11,R29,R30,R31,R32 | 5 | 10K |  |  | Resistor_SMD:R_0402_1005Metric | https://www.vishay.com/docs/28773/crcwce3.pdf | 0.35 | Vishay | CRCW040210K0FKEDC | 71-CRCW040210K0FKEDC | https://www.mouser.com/ProductDetail/Vishay-Dale/CRCW040210K0FKEDC | 10K 63mW | 1V1 UVLO Rb,Pull Up Resistor
R12 | 1 | 26K7 |  |  | Resistor_SMD:R_0402_1005Metric | https://www.vishay.com/doc?20035 | 0.4 | Vishay | CRCW040226K7FKED | 71-CRCW0402-26.7K-E3 | https://www.mouser.com/ProductDetail/Vishay-Dale/CRCW040226K7FKED | 26K7 63mW | 3V3 UVLO Rt
R13 | 1 | 10K2 |  |  | Resistor_SMD:R_0402_1005Metric | https://www.vishay.com/doc?20035 | 0.4 | Vishay | CRCW040210K2FKED | 71-CRCW0402-10.2K-E3 | https://www.mouser.com/ProductDetail/Vishay-Dale/CRCW040210K2FKED | 10K2 63mW | 1V1 UVLO Rt
R14 | 1 | 90K9 |  |  | Resistor_SMD:R_0402_1005Metric | https://www.vishay.com/docs/28758/tnpw_e3.pdf | 0.4 | Vishay | TNPW040290K9BEED | 71-TNPW040290K9BEED | https://www.mouser.com/ProductDetail/Vishay-Dale/TNPW040290K9BEED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 | 90K9 130mW | Vbus Sense Resistor Top
R15 | 1 | 10K |  |  | Resistor_SMD:R_0402_1005Metric | https://www.vishay.com/docs/28758/tnpw_e3.pdf | 0.4 | Vishay | TNPW040210K0BEED | 71-TNPW040210K0BEED | https://www.mouser.com/ProductDetail/Vishay-Dale/TNPW040210K0BEED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 | 10K 130mW | Vbus Sense Resistor Bottom
R16,R17,R21,R22,R23,R24,R26,R27 | 8 | 4K7 |  |  | Resistor_SMD:R_0402_1005Metric | https://www.vishay.com/docs/28773/crcwce3.pdf | 0.35 | Vishay | CRCW04024K70FKEDC | 71-CRCW04024K70FKEDC | https://www.mouser.com/ProductDetail/Vishay-Dale/CRCW04024K70FKEDC | 4K7 63mW | Pull Down Resistor,Pull Up Resistor
R18,R19,R20 | 3 | 1M |  |  | Resistor_SMD:R_0402_1005Metric | https://www.vishay.com/docs/28773/crcwce3.pdf | 0.35 | Vishay | CRCW04021M00FKED | 71-CRCW0402-1.0M-E3 | https://www.mouser.com/ProductDetail/Vishay-Dale/CRCW04021M00FKED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 | 1M 63mW | Pull Down Resistor
R25 | 1 | 9K53 |  |  | Resistor_SMD:R_0402_1005Metric | https://www.vishay.com/docs/28758/tnpw_e3.pdf | 0.4 | Vishay | TNPW04029K53BEED | 71-TNPW04029K53BEED | https://www.mouser.com/ProductDetail/Vishay-Dale/TNPW04029K53BEED?qs=Gz84PCHjosD8f58lgDAq1A%3D%3D | 9K53 130mW | USB Ref Resistor
R28,R33 | 2 | 25K5 |  |  | Resistor_SMD:R_0402_1005Metric | https://www.vishay.com/docs/28758/tnpw_e3.pdf | 0.4 | Vishay | TNPW040225K5BEED | 71-TNPW040225K5BEED | https://www.mouser.com/ProductDetail/Vishay-Dale/TNPW040225K5BEED?qs=wTZ%2FFzl837ZLdDCLi1n5vA%3D%3D | 25K5 130mW | Current Limit Resistor
R34,R35 | 2 | 3K9 |  |  | Resistor_SMD:R_0402_1005Metric | https://www.vishay.com/docs/28773/crcwce3.pdf | 0.35 | Vishay | CRCW04023K90FKED | 71-CRCW04023K90FKED | https://www.mouser.com/ProductDetail/Vishay-Dale/CRCW04023K90FKED | 3K9 63mW | I2C Pull Up Resistor
U1 | 1 | LM64440APPQRYFRQ1 |  |  | DW_Semiconductors:[U] TI LM63460 Sw Volt Reg | https://www.ti.com/lit/ds/symlink/lm64440-q1.pdf?ts=1744413173548 | 1.05 | Texas Instruments | LM64440APPQRYFRQ1 | 595-LM64440APPQRYRQ1 | https://www.mouser.com/ProductDetail/Texas-Instruments/LM64440APPQRYFRQ1?qs=iLKYxzqNS76Y4Mk8QuxuqQ%3D%3D | 4A 2.1MHz | Switching Voltage Regulators Automotive 3V to 36 V 4A low-EMI synchronous
U2 | 1 | TLV75511PDQNR |  |  | DW_Semiconductors:[U] TI LDO Regulator TLV755 DQN | https://www.ti.com/lit/gpn/tlv755p | 0.4 | Texas Instruments | TLV75511PDQNR | 595-TLV75511PDQNR | https://www.mouser.com/ProductDetail/Texas-Instruments/TLV75511PDQNR?qs=w%2Fv1CP2dgqp0zobivtVyXQ%3D%3D | 0.5A 1.1V Output LDO | LDO Voltage Regulators 500-mA high-PSRR low -IQ low-dropout
U3 | 1 | TLV75533PDQNR |  |  | DW_Semiconductors:[U] TI LDO Regulator TLV755 DQN | https://www.ti.com/lit/gpn/tlv755p | 0.4 | Texas Instruments | TLV75533PDQNR | 595-TLV75533PDQNR | https://www.mouser.com/ProductDetail/Texas-Instruments/TLV75533PDQNR?qs=55YtniHzbhD4SvMoS6ilhA%3D%3D | 0.5A 3.3V Output LDO | LDO Voltage Regulators 500-mA high-PSRR low -IQ low-dropout
U4 | 1 | TUSB4041IPAPR |  |  | DW_Semiconductors:[U] Texas Inst USB 2.0 Hub Controller TUSB4041I QFP50P1200X1200X120-65N | http://www.ti.com/general/docs/lit/getliterature.tsp?genericPartNumber=TUSB4041I&&fileType=pdf | 1.2 | Texas Instruments | TUSB4041IPAPR | 595-TUSB4041IPAPR | https://www.mouser.co.uk/ProductDetail/Texas-Instruments/TUSB4041IPAPR?qs=UPLqB4C8V4FMJLHct9f9fw%3D%3D | TUSB4041IPAPR | TEXAS INSTRUMENTS - TUSB4041IPAPR - USB 2.0 HUB, 480MBPS, HTQFP-64
U5,U6 | 2 | TPS2561DRCR |  |  | DW_Semiconductors:[U] TI USB Power Ctlr TPS2561DRCR | https://www.ti.com/lit/gpn/TPS2561 | 1 | Texas Instruments | TPS2561DRCR | 595-TPS2561DRCR | https://www.mouser.co.uk/ProductDetail/Texas-Instruments/TPS2561DRCR?qs=%2Fqzd9s%252BcLd7rIDSRKlRjAw%3D%3D | TPS2561DRCR | Power Switch ICs - Power Distribution Dual Ch Prec Adj Current-Ltd Pwr Sw
U7 | 1 | CAT24C32HU4I-GT3 |  |  | DW_Semiconductors:[U] OnSemi Serial EEPROM 4KB CAT24C32HU4I-GT3 | https://www.onsemi.com/download/data-sheet/pdf/cat24c32-d.pdf | 0.55 | OnSemi | CAT24C32HU4I-GT3 | 863-CAT24C32HU4I-GT3 | https://www.mouser.com/ProductDetail/onsemi/CAT24C32HU4I-GT3?qs=2mdvTlUeTfA3f6AaECTBOg%3D%3D | CAT24C32HU4I-GT3 | Supports Standard, Fast and Fast-Plus I2C Protocol; 1.7 V to 5.5 V Supply Voltage Range; 32-Byte Page Write Buffer; Hardware Write Protection for entire memory; Schmitt Triggers and Noise Suppression Filters on IC Bus Inputs (SCL and SDA); Low power CMOS technology; 1,000,000 program/erase cycles; 100 year data retention; 8-lead SOIC and TSSOP, WLCSP 4 and 5-ball and 8-pad UDFN packages; Industrial temperature range; This Device is PbFree, Halogen Free/BFR Free, and RoHS Compliant
U8,U9,U10,U11,U12 | 5 | USBLC6-2P6 |  |  | DW_Semiconductors:[U] ST Micro USB ESD Protection USBLC6-2P6 | https://www.mouser.com/datasheet/2/389/usblc6_2-1852789.pdf | 0.6 | STMicroelectronics | USBLC6-2P6 | 511-USBLC6-2P6 | https://www.mouser.com/ProductDetail/STMicroelectronics/USBLC6-2P6?qs=6ARB0lp6jlViGcbUSvj1Mw%3D%3D | USBLC6-2P6 | ESD Suppressors / TVS Diodes High Speed Interface Protection Low Cap
Y1 | 1 | ECS-2520MV-240-BL-TR |  |  | DW_Semiconductors:[Y] ECS Clock Osc 24MHz ECS2520MV240BLTR | https://ecsxtal.com/store/pdf/ECS-2520MV.pdf | 0.9 | ECS | ECS-2520MV-240-BL-TR | 520-2520MV-240-BL-TR | https://www.mouser.com/ProductDetail/ECS/ECS-2520MV-240-BL-TR?qs=DRkmTr78QAT9UStHJvO4kg%3D%3D | ECS-2520MV-240-BL-TR | Standard Clock Oscillators 24.000 MHz Multi-Volt 1.6 3.6V +/-50 ppm -10 +70 C 4-SMD 2.5x2.0mm RoHS
Wire-to-Board Connector | 2 | XHP-2 |  |  |  | https://www.mouser.com/datasheet/2/564/eXH-3476786.pdf | 7.5 | JST | XHP-2 | 306-XHP-2 | https://www.mouser.com/ProductDetail/JST-Commercial/XHP-2?qs=QpmGXVUTftGT4osVcj8ZRw%3D%3D | JST-XH-2 Wire Connector | 1 for fan plug, one for power plug
Wire-to-Board Crimp Fitting | 4 | SXH-001T-P0.6 |  |  |  | https://www.mouser.com/datasheet/2/564/eXH-3476786.pdf | - | JST | SXH-001T-P0.6 | 306-SXH-001T-P0.6 | https://www.mouser.com/ProductDetail/JST-Commercial/SXH-001T-P0.6?qs=QpmGXVUTftHVe8yFBLIwfA%3D%3D | Wire crimp inserts - 2 for fan, 2 for input power
Misc Hardware | 4 |  |  |  |  |  |  |  |  |  | https://www.amazon.com/dp/B01N5RDAUX |  | M2.5 x 6mm phillips pan-head mounting screws
Misc Hardware | 4 |  |  |  |  |  |  |  |  |  | ^^^ Included in above kit |  | Brass PCB standoffs, 20mm standoff + 6mm M2.5 threaded extension
Misc Hardware | 3 |  |  |  |  |  |  |  |  |  | ^^^ Included in above kit |  | M2.5 hex nut
Misc Hardware | 3 |  |  |  |  |  |  |  |  |  | https://www.amazon.com/mxuteuk-Assortment-Stainless-Assorted-G035-M2-5/dp/B0D7ZZ7J17 |  | M2.5 x 16mm hex cap screws for fan
Misc Hardware | 1 |  |  |  |  |  |  |  |  |  | https://www.amazon.com/dp/B0CTX2PRYF |  | 6mm x 6mm x 5mm copper heat sink for power regulator
Misc Hardware | 1 |  |  |  |  |  |  |  |  |  | https://www.amazon.com/dp/B000067RMY |  | USB A-B cable, 6 in / 15 cm

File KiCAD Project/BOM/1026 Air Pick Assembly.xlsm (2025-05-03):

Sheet: Parts List
1026 Rpi Power Hat
Air Pick Assembly |  |  |  |  |  |  | Smallest Dim
 |  |  |  | Tape | Mark | Mark | Size | Size | AirPick
Reference | Qty | Manufacturer_Part_Number | Spec | Width | Code | Symb | mm | mil | Tip | Tape | Notes
C1,C2 | 2 | T521D336M035ATE065 | 33u 35V | 12 | B | â | 4 |  | 1/8 |  | Mark = +
L1 | 1 | LPS4040-223 | 22uH 0.8A 210mohm | 12 | N | ¡ | 4 |  | 1/8
L2 | 1 | XGL4025-152ME | 1.5u 8A 11mohm | 12 | N | ¡ | 4 |  | 1/8
U1 | 1 | LM64440APPQRYFRQ1 | 4A 2.1MHz | 12 | TL | ã | 4.1 |  | 1/8
D2 | 1 | 150040GS73220 | 0603 525nm | 8 | T | á | 0.5 |  | 1005 |  | Mark = Cathode
D4 | 1 | 150040RS73240 | 0402 630nm | 8 | T | á | 0.5 |  | 1005 |  | Mark = Cathode
C12 | 1 | GRM0225C1C100FA03L | 10p 16V C0G | 8 | N | ¡ |  | 20 | 2010
C30,C33,C35 | 3 | GCM155R71H104KE02J | 100n 50V | 8 | N | ¡ |  | 20 | 2010
C31,C32,C34 | 3 | GCM155R71H102KA37D | 1n 50V | 8 | N | ¡ |  | 20 | 2010
C5,C6 | 2 | GCM155R71H223KA55D | 22n 50V | 8 | N | ¡ |  | 20 | 2010
C8,C9,C17,C18,C19,C20,C22,C23,C24,C25,C26,C27,C28,C37,C38,C39,C42,C43,C45,C47,C48,C49,C50,C51,C52 | 25 | GCM155R71C104KA55D | 100n 16V | 8 | N | ¡ |  | 20 | 2010
FB1,FB2 | 2 | BLM15PX221SZ1D | 220 ohm 100MHz | 8 | N | ¡ |  | 20 | 2010
R1 | 1 | CRCW040215K0FKED | 15K 63mW | 8 | N | ¡ |  | 20 | 2010
R10 | 1 | CRCW040212K7FKED | 12K7 63mW | 8 | N | ¡ |  | 20 | 2010
R11,R29,R30,R31,R32 | 5 | CRCW040210K0FKEDC | 10K 63mW | 8 | N | ¡ |  | 20 | 2010
R12 | 1 | CRCW040226K7FKED | 26K7 63mW | 8 | N | ¡ |  | 20 | 2010
R13 | 1 | CRCW040210K2FKED | 10K2 63mW | 8 | N | ¡ |  | 20 | 2010
R14 | 1 | TNPW040290K9BEED | 90K9 130mW | 8 | N | ¡ |  | 20 | 2010
R15 | 1 | TNPW040210K0BEED | 10K 130mW | 8 | N | ¡ |  | 20 | 2010
R16,R17,R21,R22,R23,R24,R26,R27 | 8 | CRCW04024K70FKEDC | 4K7 63mW | 8 | N | ¡ |  | 20 | 2010
R18,R19,R20 | 3 | CRCW04021M00FKED | 1M 63mW | 8 | N | ¡ |  | 20 | 2010
R2 | 1 | CRCW040247K0FKED | 47K 63mW | 8 | N | ¡ |  | 20 | 2010
R25 | 1 | TNPW04029K53BEED | 9K53 130mW | 8 | N | ¡ |  | 20 | 2010
R28,R33 | 2 | TNPW040225K5BEED | 25K5 130mW | 8 | N | ¡ |  | 20 | 2010
R3 | 1 | CRCW040295K3FKED | 95K3 63mW | 8 | N | ¡ |  | 20 | 2010
R34,R35 | 2 | CRCW04023K90FKED | 3K9 63mW | 8 | N | ¡ |  | 20 | 2010
R4 | 1 | CRCW04026K34FKEDC | 6K34 63mW | 8 | N | ¡ |  | 20 | 2010
R5 | 1 | CRCW04024R70FNED | 4R7 63mW | 8 | N | ¡ |  | 20 | 2010
R6 | 1 | TNPW040256K2BEED | 56K2 130mW | 8 | N | ¡ |  | 20 | 2010
R7 | 1 | TNPW04021K00BEED | 1K 130mW | 8 | N | ¡ |  | 20 | 2010
R8 | 1 | TNPW040213K7BEED | 13K7 130mW | 8 | N | ¡ |  | 20 | 2010
R9 | 1 | RCC04027K50FKED | 7K5 125mW | 8 | N | ¡ |  | 20 | 2010
C10,C11 | 2 | GCM32ER71C226ME19L | 22u 16V | 8 | N | ¡ |  | 100 | 3/32
C3,C4 | 2 | GRJ32ER71H106KE11K | 10u 50V | 8 | N | ¡ |  | 100 | 3/32
C40,C41,C44,C46 | 4 | TCJB157M006R0070 | 150u 6V3 | 8 | B | â |  | 100 | 3/32 |  | Mark = +
F1 | 1 | 1812L110/33MR | 1.1A 33V | 12 | N | ¡ | 3.07 |  | 3/32
U5,U6 | 2 | TPS2561DRCR | TPS2561DRCR | 12 | TR | ä | 3.1 |  | 3/32
U4 | 1 | TUSB4041IPAPR | TUSB4041IPAPR | 24 | TR | ä | 10.2 |  | 3/8
C7,C13,C14,C15,C16,C36 | 6 | GCM188R71C105KA64J | 1u 16V | 8 | N | ¡ |  | 30 | 3020
FB3,FB4,FB5,FB6 | 4 | BLM18KG221SN1D | 220ohm 2.2A | 8 | N | ¡ |  | 30 | 3020
U2 | 1 | TLV75511PDQNR | 0.5A 1.1V Output LDO | 8 | TR | ä | 1 |  | 3020
U3 | 1 | TLV75533PDQNR | 0.5A 3.3V Output LDO | 8 | TR | ä | 1 |  | 3020
C21,C29 | 2 | GCM21BR70J106KE22K | 10u 6V3 | 8 | N | ¡ |  | 50 | 4030
D1 | 1 | PDZ10B,115 | 10V 2% 400mW | 8 | T | á | 1.15 |  | 4030 |  | Mark = Cathode
D3 | 1 | SMF24CA | TVS BiDir 24V 200W | 8 | N | ¡ | 1.5 |  | 4030
U8,U9,U10,U11,U12 | 5 | USBLC6-2P6 | USBLC6-2P6 | 8 | BL | å | 1.5 |  | 4030
Q1 | 1 | BUK6D120-60PX | P-Ch 60V 8A | 8 | TR | ä | 2 |  | 6040
U7 | 1 | CAT24C32HU4I-GT3 | CAT24C32HU4I-GT3 | 8 | TR | ä | 2 |  | 6040
Y1 | 1 | ECS-2520MV-240-BL-TR | ECS-2520MV-240-BL-TR | 8 | TL | ã | 2 |  | 6040

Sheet: AirPick Tips
AirPick Tips
Outer | Outer |  | Orientation
Mil | Tnths mm | Tip ID | Code | Symbol
8 | 2.032 | 0803 | N | ¡
10 | 2.540 | 1005 | T | á
20 | 5.080 | 2010 | TR | ä
30 | 7.620 | 3020 | R | à
40 | 10.160 | 4030 | BR | æ
60 | 15.240 | 6040 | B | â
80 | 20.320 | 8060 | BL | å
94 | 23.876 | 3/32 | L | ß
125 | 31.750 | 1/8 | TL | ã
250 | 63.500 | 1/4
375 | 95.250 | 3/8
500 | 127.000 | 1/2

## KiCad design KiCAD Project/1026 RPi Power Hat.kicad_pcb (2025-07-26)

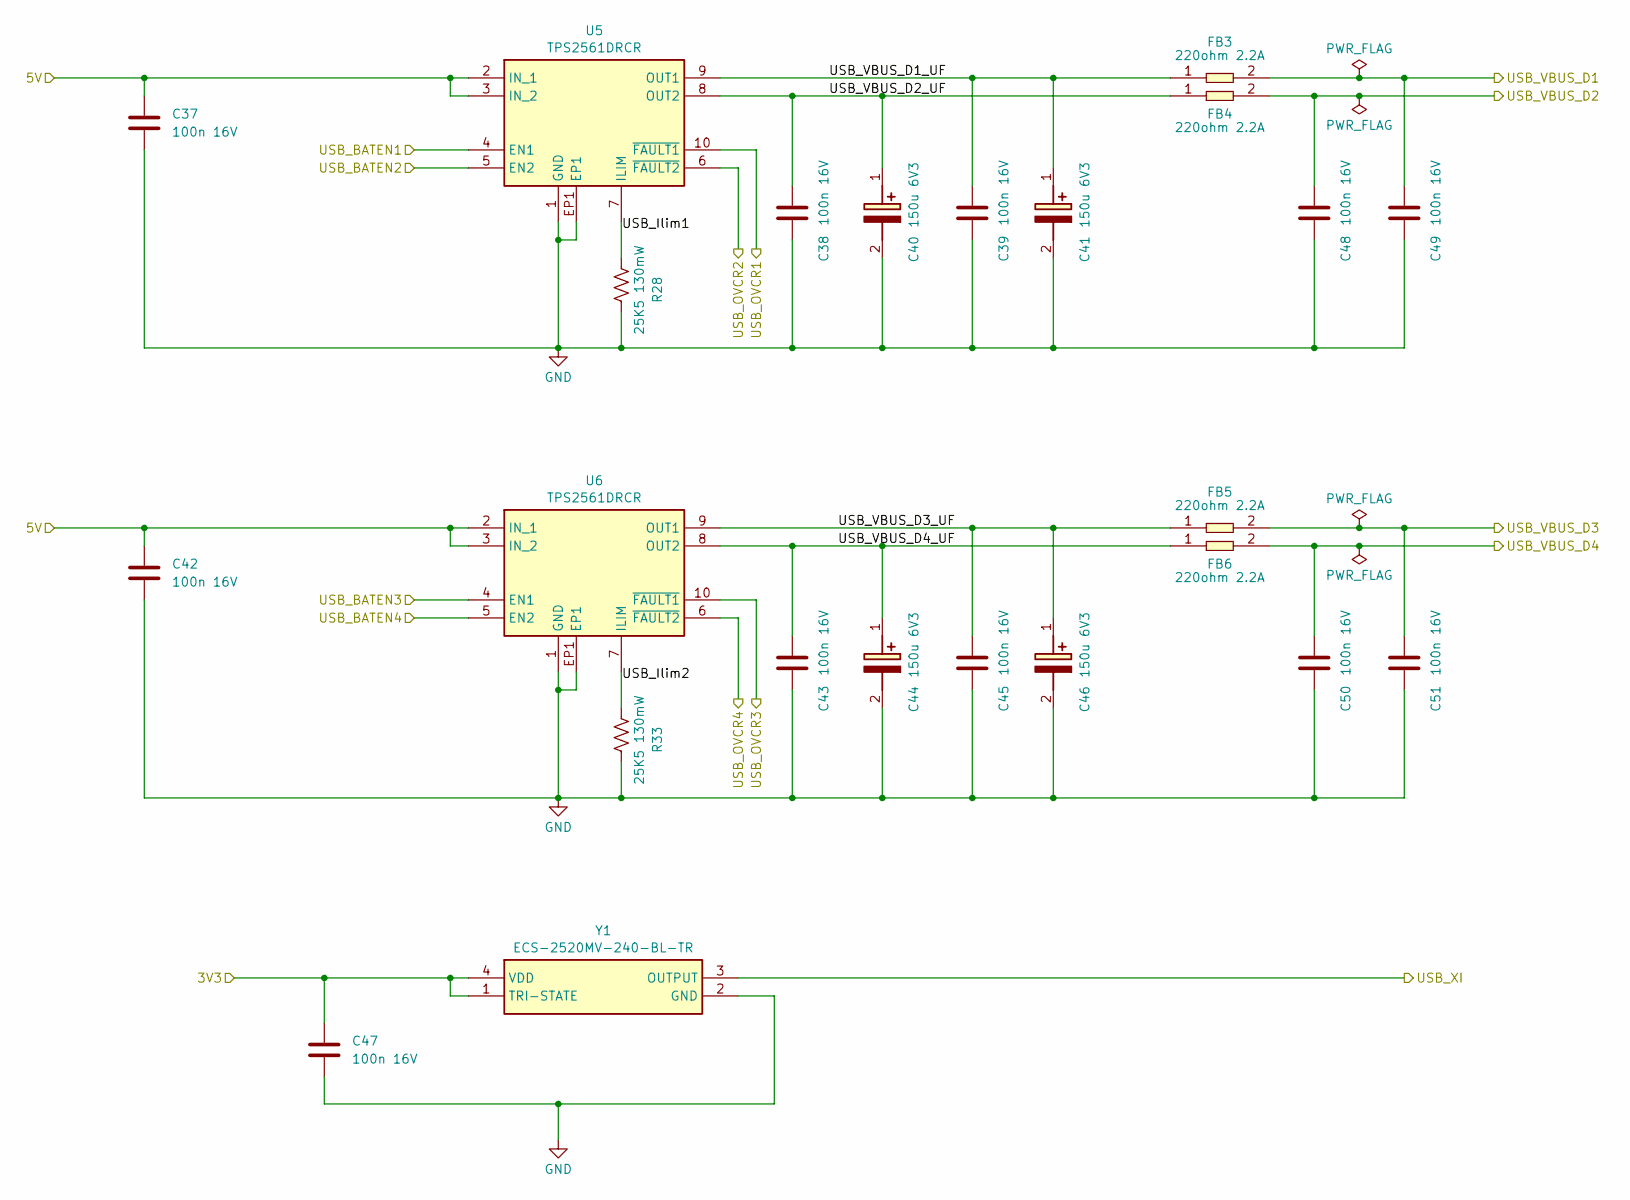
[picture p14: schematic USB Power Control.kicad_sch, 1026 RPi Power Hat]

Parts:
C37, C38, C39, C42, C43, C45, C47, C48, C49, C50, C51: GCM155R71C104KA55D; C_0402_1005Metric; Manufacturer_Part_Number GCM155R71C104KA55D; Mouser Part Number 81-GCM155R71C104KA5D
C40, C41, C44, C46: TCJB157M006R0070; [C] Kyocera AVC Tant Poly TCJB157M006R0070; Mouser Part Number 581-TCJB157M006R0070
FB3, FB4, FB5, FB6: BLM18KG221SN1D; [FB] Murata BLM18KG221SN1D 220ohm 2.2A; Mouser Part Number 81-BLM18KG221SN1D
R28, R33: 25K5; R_0402_1005Metric; Manufacturer_Part_Number TNPW040225K5BEED; Mouser Part Number 71-TNPW040225K5BEED
U5, U6: TPS2561DRCR; [U] TI USB Power Ctlr TPS2561DRCR; Mouser Part Number 595-TPS2561DRCR
Y1: ECS-2520MV-240-BL-TR; [Y] ECS Clock Osc 24MHz ECS2520MV240BLTR; Mouser Part Number 520-2520MV-240-BL-TR

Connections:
/5V Regulator/5V: C37.2, C42.2, U5.2 (IN_1), U5.3 (IN_2), U6.2 (IN_1), U6.3 (IN_2); also elsewhere on the board
/Fan / Header / GPIO / EEPROM/3V3: C47.2, Y1.1 (TRI-STATE), Y1.4 (VDD); also elsewhere on the board
/USB ESD Protection/USB_VBUS_D1: C49.2, FB3.2; also elsewhere on the board
/USB ESD Protection/USB_VBUS_D2: C48.2, FB4.2; also elsewhere on the board
/USB ESD Protection/USB_VBUS_D3: C51.2, FB5.2; also elsewhere on the board
/USB ESD Protection/USB_VBUS_D4: C50.2, FB6.2; also elsewhere on the board
/USB Hub/USB_BATEN1: U5.4 (EN1); also elsewhere on the board
/USB Hub/USB_BATEN2: U5.5 (EN2); also elsewhere on the board
/USB Hub/USB_BATEN3: U6.4 (EN1); also elsewhere on the board
/USB Hub/USB_BATEN4: U6.5 (EN2); also elsewhere on the board
/USB Hub/USB_OVCR1: U5.10 (~FAULT1); also elsewhere on the board
/USB Hub/USB_OVCR2: U5.6 (~FAULT2); also elsewhere on the board
/USB Hub/USB_OVCR3: U6.10 (~FAULT1); also elsewhere on the board
/USB Hub/USB_OVCR4: U6.6 (~FAULT2); also elsewhere on the board
/USB Hub/USB_XI: Y1.3 (OUTPUT); also elsewhere on the board
/USB Power Control/USB_Ilim1: R28.1, U5.7 (ILIM)
/USB Power Control/USB_Ilim2: R33.1, U6.7 (ILIM)
/USB Power Control/USB_VBUS_D1_UF: C39.2, C41.1 (+), FB3.1, U5.9 (OUT1)
/USB Power Control/USB_VBUS_D2_UF: C38.2, C40.1 (+), FB4.1, U5.8 (OUT2)
/USB Power Control/USB_VBUS_D3_UF: C45.2, C46.1 (+), FB5.1, U6.9 (OUT1)
/USB Power Control/USB_VBUS_D4_UF: C43.2, C44.1 (+), FB6.1, U6.8 (OUT2)
GND: C37.1, C38.1, C39.1, C40.2 (-), C41.2 (-), C42.1, C43.1, C44.2 (-), C45.1, C46.2 (-), C47.1, C48.1, C49.1, C50.1, C51.1, R28.2, R33.2, U5.1 (GND), U5.EP1, U6.1 (GND), U6.EP1, Y1.2 (GND); also elsewhere on the board

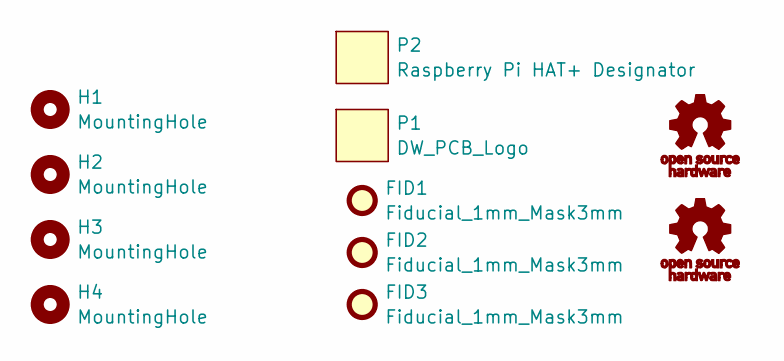
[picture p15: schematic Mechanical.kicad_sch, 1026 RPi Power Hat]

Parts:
FID1, FID2, FID3: Fiducial_1mm_Mask3mm; Fiducial_1mm_Mask2mm
G1, G2: OSHW_Logo
H1, H4: MountingHole; [MH] MountingHole_2.7mm_M2.5
H2, H3: MountingHole; [MH] MountingHole_2.7mm_M2.5_StencilRegHole
P1: DW_PCB_Logo
P2: Raspberry Pi HAT+ Designator; [G] RPi HAT+ Designator

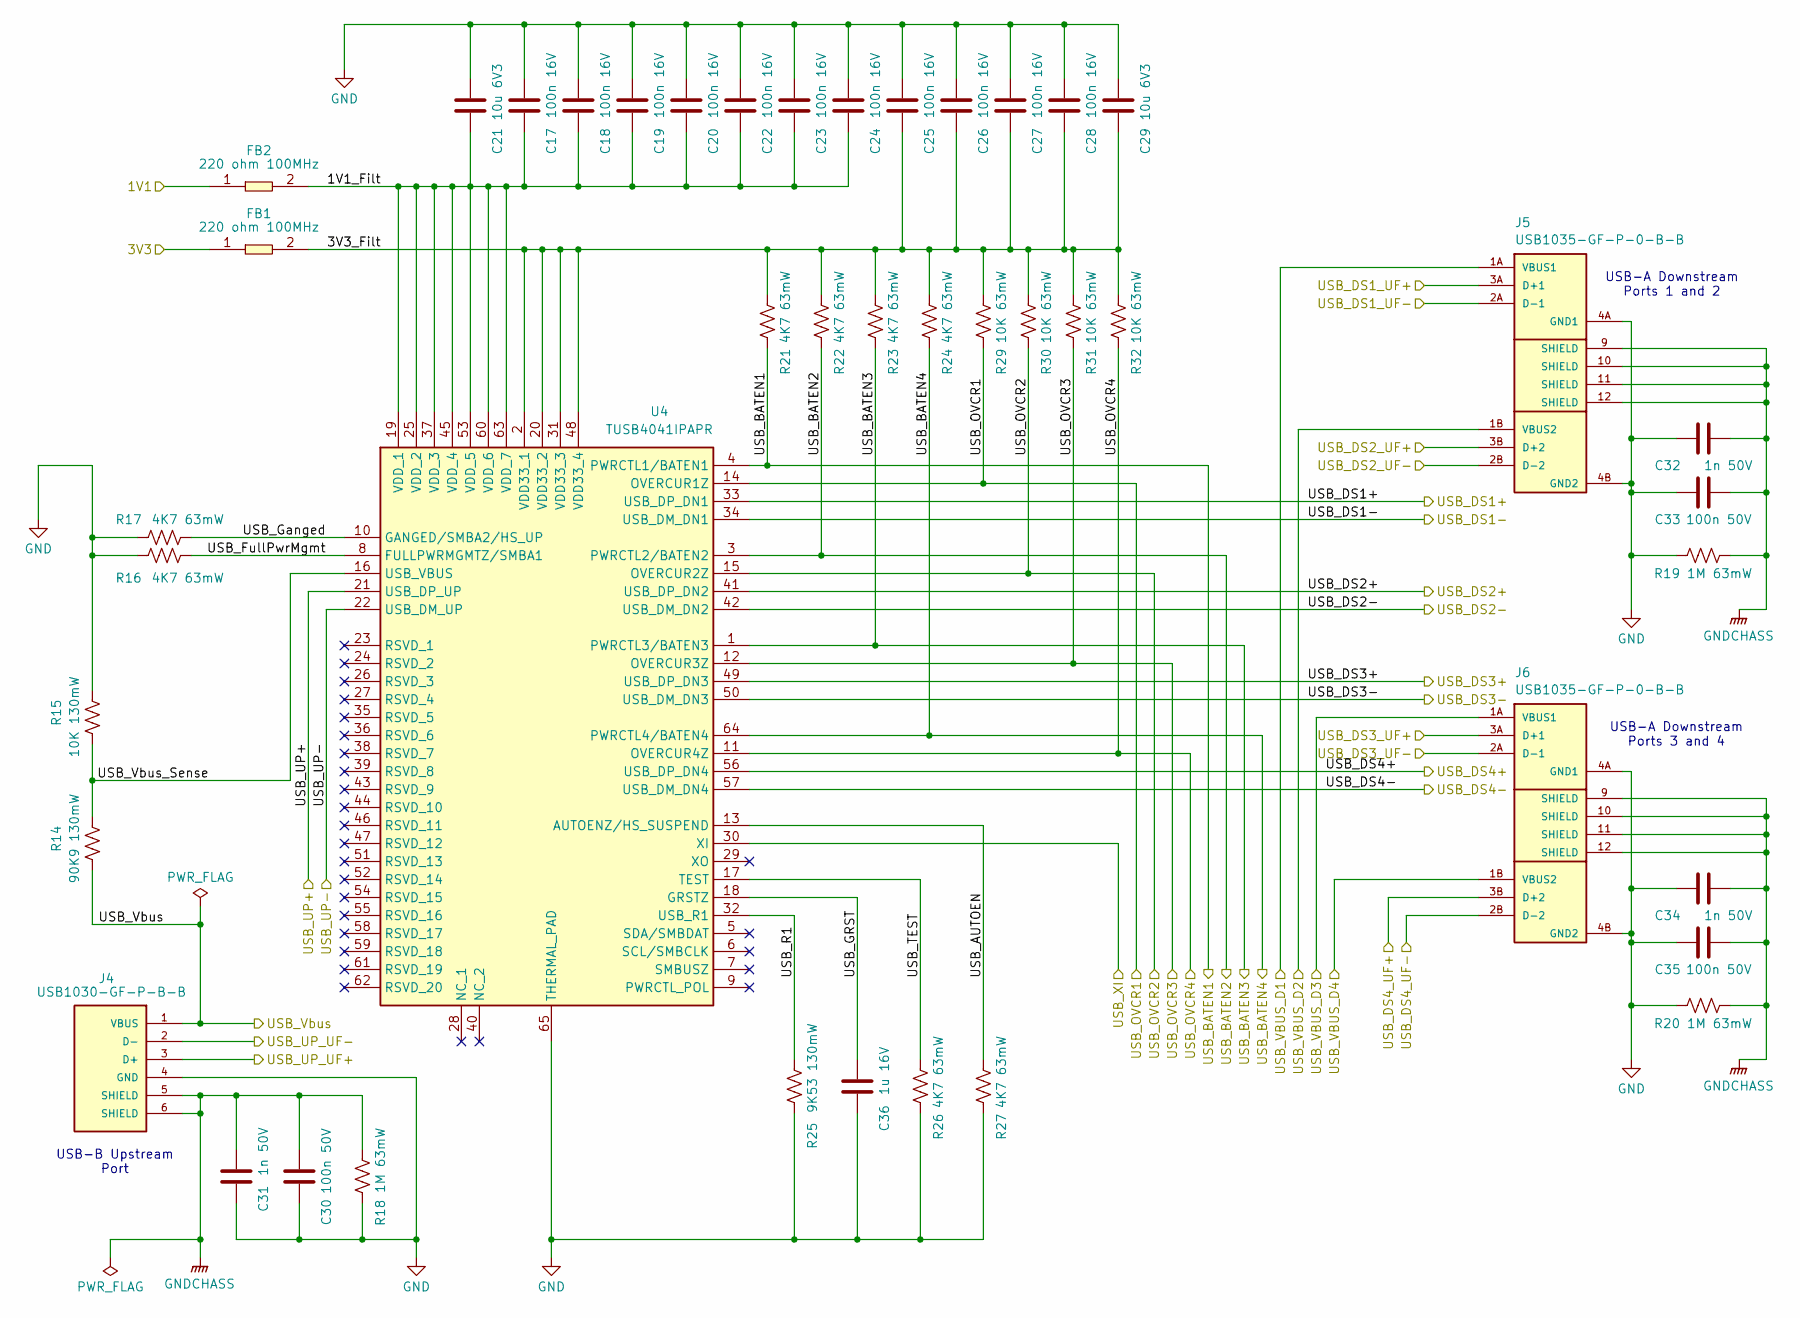
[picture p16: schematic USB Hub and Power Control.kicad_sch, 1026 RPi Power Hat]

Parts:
C17, C18, C19, C20, C22, C23, C24, C25, C26, C27, C28: GCM155R71C104KA55D; C_0402_1005Metric; Manufacturer_Part_Number GCM155R71C104KA55D; Mouser Part Number 81-GCM155R71C104KA5D
C21, C29: GCM21BR70J106KE22K; C_0805_2012Metric; Manufacturer_Part_Number GCM21BR70J106KE22K; Mouser Part Number 81-GCM21BR70J106KE2K
C30, C33, C35: GCM155R71H104KE02J; C_0402_1005Metric; Manufacturer_Part_Number GCM155R71H104KE02J; Mouser Part Number 81-GCM155R71H104KE2J
C31, C32, C34: GCM155R71H102KA37D; C_0402_1005Metric; Manufacturer_Part_Number GCM155R71H102KA37D; Mouser Part Number 81-GCM155R71H102KA7D
C36: GCM188R71C105KA64J; C_0603_1608Metric; Manufacturer_Part_Number GCM188R71C105KA64J; Mouser Part Number 81-GCM188R71C105KA4J
FB1, FB2: BLM15PX221SZ1D; [FB] Murata BLM15PX221SZ1D; Mouser Part Number 81-BLM15PX221SZ1D
J4: USB1030-GF-P-B-B; [J] GCT USB-B 2.0 Connector PCB USB1030-GF-P-B-B; Manufacturer_Part_Number USB1030-GF-P-B-B; Mouser Part Number 640-USB1030-GF-P-B-B
J5, J6: USB1035-GF-P-0-B-B; [J] GCT USB-A x2 2.0 Connector USB1035-GF-P-0-B-B; Manufacturer_Part_Number USB1035-GF-P-0-B-B; Mouser Part Number 640-USB1035GFP0BB
R14: 90K9; R_0402_1005Metric; Manufacturer_Part_Number TNPW040290K9BEED; Mouser Part Number 71-TNPW040290K9BEED
R15: 10K; R_0402_1005Metric; Manufacturer_Part_Number TNPW040210K0BEED; Mouser Part Number 71-TNPW040210K0BEED
R16, R17, R21, R22, R23, R24, R26, R27: 4K7; R_0402_1005Metric; Manufacturer_Part_Number CRCW04024K70FKEDC; Mouser Part Number 71-CRCW04024K70FKEDC
R18, R19, R20: 1M; R_0402_1005Metric; Manufacturer_Part_Number CRCW04021M00FKED; Mouser Part Number 71-CRCW0402-1.0M-E3
R25: 9K53; R_0402_1005Metric; Manufacturer_Part_Number TNPW04029K53BEED; Mouser Part Number 71-TNPW04029K53BEED
R29, R30, R31, R32: 10K; R_0402_1005Metric; Manufacturer_Part_Number CRCW040210K0FKEDC; Mouser Part Number 71-CRCW040210K0FKEDC
U4: TUSB4041IPAPR; [U] Texas Inst USB 2.0 Hub Controller TUSB4041I QFP50P1200X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; Mouser Part Number 595-TUSB4041IPAPR

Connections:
/Fan / Header / GPIO / EEPROM/3V3: FB1.1; also elsewhere on the board
/Linear Regulators/1V1: FB2.1; also elsewhere on the board
/USB ESD Protection/USB_DS1_UF+: J5.3A (D+1); also elsewhere on the board
/USB ESD Protection/USB_DS1_UF-: J5.2A (D-1); also elsewhere on the board
/USB ESD Protection/USB_DS2_UF+: J5.3B (D+2); also elsewhere on the board
/USB ESD Protection/USB_DS2_UF-: J5.2B (D-2); also elsewhere on the board
/USB ESD Protection/USB_DS3_UF+: J6.3A (D+1); also elsewhere on the board
/USB ESD Protection/USB_DS3_UF-: J6.2A (D-1); also elsewhere on the board
/USB ESD Protection/USB_DS4_UF+: J6.3B (D+2); also elsewhere on the board
/USB ESD Protection/USB_DS4_UF-: J6.2B (D-2); also elsewhere on the board
/USB ESD Protection/USB_UP_UF+: J4.3 (D+); also elsewhere on the board
/USB ESD Protection/USB_UP_UF-: J4.2 (D-); also elsewhere on the board
/USB ESD Protection/USB_VBUS_D1: J5.1A (VBUS1); also elsewhere on the board
/USB ESD Protection/USB_VBUS_D2: J5.1B (VBUS2); also elsewhere on the board
/USB ESD Protection/USB_VBUS_D3: J6.1A (VBUS1); also elsewhere on the board
/USB ESD Protection/USB_VBUS_D4: J6.1B (VBUS2); also elsewhere on the board
/USB Hub/1V1_Filt: C17.1, C18.1, C19.1, C20.1, C21.2, C22.1, C23.1, C24.1, FB2.2, U4.19 (VDD_1), U4.25 (VDD_2), U4.37 (VDD_3), U4.45 (VDD_4), U4.53 (VDD_5), U4.60 (VDD_6), U4.63 (VDD_7)
/USB Hub/3V3_Filt: C25.1, C26.1, C27.1, C28.1, C29.2, FB1.2, R21.2, R22.2, R23.2, R24.2, R29.2, R30.2, R31.2, R32.2, U4.2 (VDD33_1), U4.20 (VDD33_2), U4.31 (VDD33_3), U4.48 (VDD33_4)
/USB Hub/USB_AUTOEN: R27.2, U4.13 (AUTOENZ/HS_SUSPEND)
/USB Hub/USB_BATEN1: R21.1, U4.4 (PWRCTL1/BATEN1); also elsewhere on the board
/USB Hub/USB_BATEN2: R22.1, U4.3 (PWRCTL2/BATEN2); also elsewhere on the board
/USB Hub/USB_BATEN3: R23.1, U4.1 (PWRCTL3/BATEN3); also elsewhere on the board
/USB Hub/USB_BATEN4: R24.1, U4.64 (PWRCTL4/BATEN4); also elsewhere on the board
/USB Hub/USB_DS1+: U4.33 (USB_DP_DN1); also elsewhere on the board
/USB Hub/USB_DS1-: U4.34 (USB_DM_DN1); also elsewhere on the board
/USB Hub/USB_DS2+: U4.41 (USB_DP_DN2); also elsewhere on the board
/USB Hub/USB_DS2-: U4.42 (USB_DM_DN2); also elsewhere on the board
/USB Hub/USB_DS3+: U4.49 (USB_DP_DN3); also elsewhere on the board
/USB Hub/USB_DS3-: U4.50 (USB_DM_DN3); also elsewhere on the board
/USB Hub/USB_DS4+: U4.56 (USB_DP_DN4); also elsewhere on the board
/USB Hub/USB_DS4-: U4.57 (USB_DM_DN4); also elsewhere on the board
/USB Hub/USB_FullPwrMgmt: R16.2, U4.8 (FULLPWRMGMTZ/SMBA1)
/USB Hub/USB_GRST: C36.1, U4.18 (GRSTZ)
/USB Hub/USB_Ganged: R17.2, U4.10 (GANGED/SMBA2/HS_UP)
/USB Hub/USB_OVCR1: R29.1, U4.14 (OVERCUR1Z); also elsewhere on the board
/USB Hub/USB_OVCR2: R30.1, U4.15 (OVERCUR2Z); also elsewhere on the board
/USB Hub/USB_OVCR3: R31.1, U4.12 (OVERCUR3Z); also elsewhere on the board
/USB Hub/USB_OVCR4: R32.1, U4.11 (OVERCUR4Z); also elsewhere on the board
/USB Hub/USB_R1: R25.2, U4.32 (USB_R1)
/USB Hub/USB_TEST: R26.2, U4.17 (TEST)
/USB Hub/USB_UP+: U4.21 (USB_DP_UP); also elsewhere on the board
/USB Hub/USB_UP-: U4.22 (USB_DM_UP); also elsewhere on the board
/USB Hub/USB_Vbus: J4.1 (VBUS), R14.1; also elsewhere on the board
/USB Hub/USB_Vbus_Sense: R14.2, R15.1, U4.16 (USB_VBUS)
/USB Hub/USB_XI: U4.30 (XI); also elsewhere on the board
GND: C17.2, C18.2, C19.2, C20.2, C21.1, C22.2, C23.2, C24.2, C25.2, C26.2, C27.2, C28.2, C29.1, C30.1, C31.1, C32.1, C33.1, C34.1, C35.1, C36.2, J4.4 (GND), J5.4A (GND1), J5.4B (GND2), J6.4A (GND1), J6.4B (GND2), R15.2, R16.1, R17.1, R18.2, R19.2, R20.2, R25.1, R26.1, R27.1, U4.65 (THERMAL_PAD); also elsewhere on the board
GNDCHASS: C30.2, C31.2, C32.2, C33.2, C34.2, C35.2, J4.5 (SHIELD), J4.6 (SHIELD), J5.9 (SHIELD), J5.10 (SHIELD), J5.11 (SHIELD), J5.12 (SHIELD), J6.9 (SHIELD), J6.10 (SHIELD), J6.11 (SHIELD), J6.12 (SHIELD), R18.1, R19.1, R20.1

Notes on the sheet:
USB-B Upstream Port
USB-A Downstream Ports 1 and 2
USB-A Downstream Ports 3 and 4

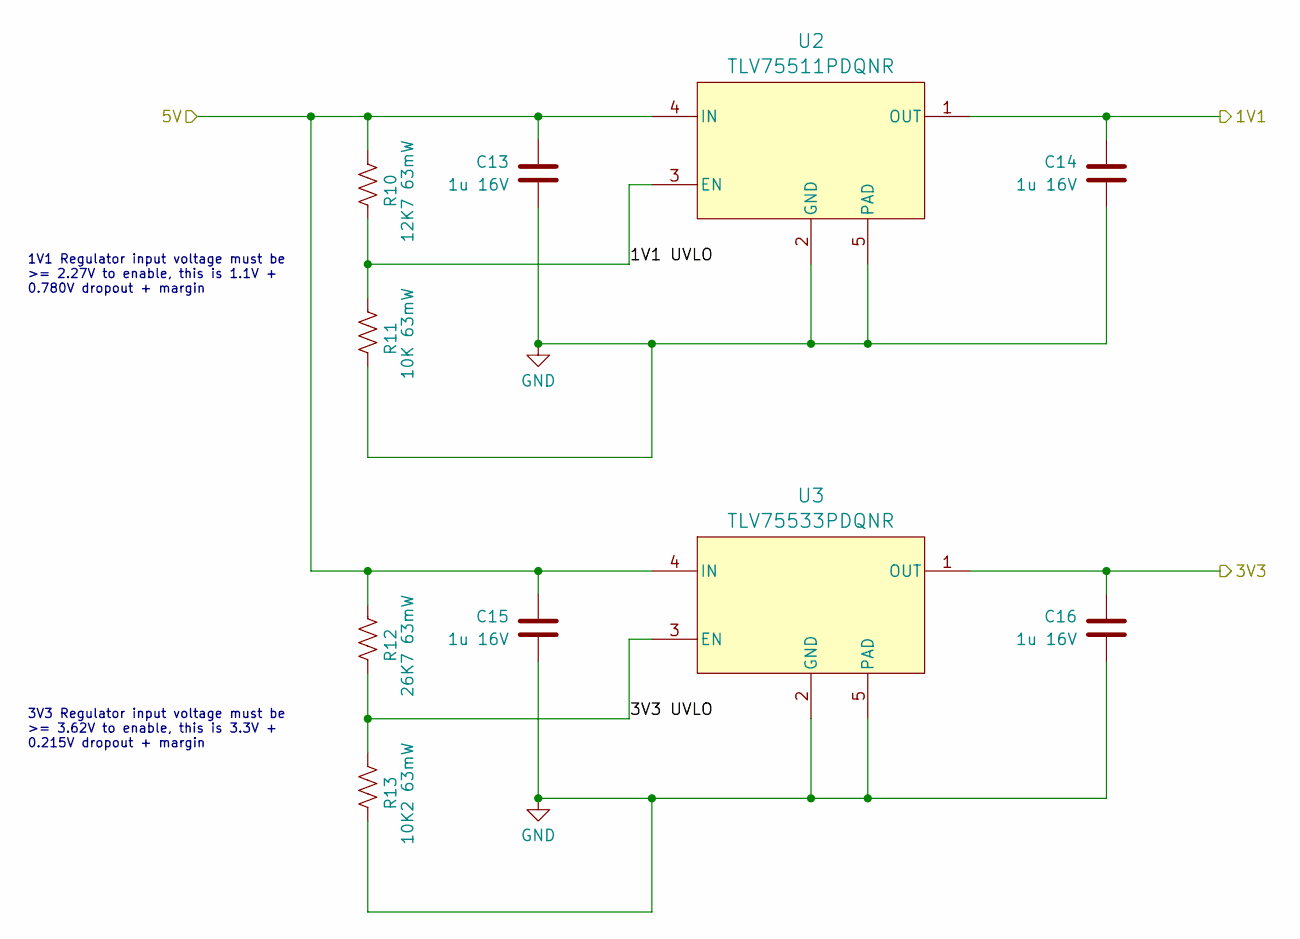
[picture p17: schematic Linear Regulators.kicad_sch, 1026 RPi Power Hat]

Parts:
C13, C14, C15, C16: GCM188R71C105KA64J; C_0603_1608Metric; Manufacturer_Part_Number GCM188R71C105KA64J; Mouser Part Number 81-GCM188R71C105KA4J
R10: 12K7; R_0402_1005Metric; Manufacturer_Part_Number CRCW040212K7FKED; Mouser Part Number 71-CRCW0402-12.7K-E3
R11: 10K; R_0402_1005Metric; Manufacturer_Part_Number CRCW040210K0FKEDC; Mouser Part Number 71-CRCW040210K0FKEDC
R12: 26K7; R_0402_1005Metric; Manufacturer_Part_Number CRCW040226K7FKED; Mouser Part Number 71-CRCW0402-26.7K-E3
R13: 10K2; R_0402_1005Metric; Manufacturer_Part_Number CRCW040210K2FKED; Mouser Part Number 71-CRCW0402-10.2K-E3
U2: TLV75511PDQNR; [U] TI LDO Regulator TLV755 DQN; Manufacturer_Part_Number TLV75511PDQNR; Mouser Part Number 595-TLV75511PDQNR
U3: TLV75533PDQNR; [U] TI LDO Regulator TLV755 DQN; Manufacturer_Part_Number TLV75533PDQNR; Mouser Part Number 595-TLV75533PDQNR

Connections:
/5V Regulator/5V: C13.1, C15.1, R10.1, R12.1, U2.4 (IN), U3.4 (IN); also elsewhere on the board
/Fan / Header / GPIO / EEPROM/3V3: C16.1, U3.1 (OUT); also elsewhere on the board
/Linear Regulators/1V1: C14.1, U2.1 (OUT); also elsewhere on the board
/Linear Regulators/1V1 UVLO: R10.2, R11.1, U2.3 (EN)
/Linear Regulators/3V3 UVLO: R12.2, R13.1, U3.3 (EN)
GND: C13.2, C14.2, C15.2, C16.2, R11.2, R13.2, U2.2 (GND), U2.5 (PAD), U3.2 (GND), U3.5 (PAD); also elsewhere on the board

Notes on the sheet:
3V3 Regulator input voltage must be >= 3.62V to enable, this is 3.3V + 0.215V dropout + margin
1V1 Regulator input voltage must be >= 2.27V to enable, this is 1.1V + 0.780V dropout + margin

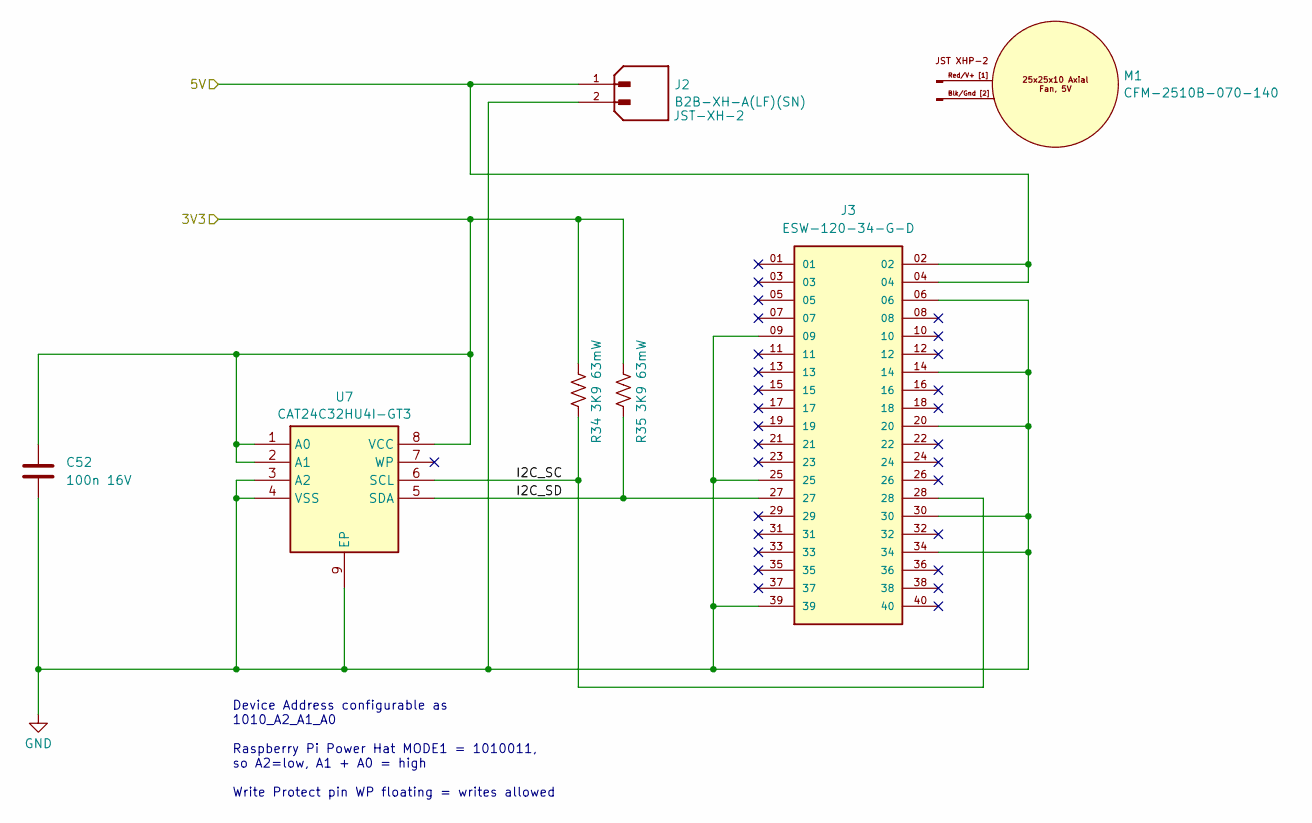
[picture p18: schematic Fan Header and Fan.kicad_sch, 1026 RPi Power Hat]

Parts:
C52: GCM155R71C104KA55D; C_0402_1005Metric; Manufacturer_Part_Number GCM155R71C104KA55D; Mouser Part Number 81-GCM155R71C104KA5D
J2: B2B-XH-A(LF)(SN); JST_B2B-XH-A(LF)(SN); Mouser Part Number 306-B2BXHALFSNP; DigiKey_Part_Number 455-B2B-XH-A-ND
J3: ESW-120-34-G-D; [J] Samtec Elevated Socket Strip ESW-120-34-G-D; Manufacturer_Part_Number ESW-120-34-G-D; Mouser Part Number 200-ESW12034GD
M1: CFM-2510B-070-140; [Fan] SameSky CFM-2510B-070-140; Manufacturer_Part_Number CFM-2510B-070-140; Mouser Part Number 490-CFM2510B-070-140
R34, R35: 3K9; R_0402_1005Metric; Manufacturer_Part_Number CRCW04023K90FKED; Mouser Part Number 71-CRCW04023K90FKED
U7: CAT24C32HU4I-GT3; [U] OnSemi Serial EEPROM 4KB CAT24C32HU4I-GT3; Mouser Part Number 863-CAT24C32HU4I-GT3

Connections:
/5V Regulator/5V: J2.1, J3.02, J3.04; also elsewhere on the board
/Fan / Header / GPIO / EEPROM/3V3: C52.2, R34.2, R35.2, U7.1 (A0), U7.2 (A1), U7.8 (VCC); also elsewhere on the board
/Fan / Header / GPIO / EEPROM/I2C_SC: J3.28, R34.1, U7.6 (SCL)
/Fan / Header / GPIO / EEPROM/I2C_SD: J3.27, R35.1, U7.5 (SDA)
GND: C52.1, J2.2, J3.06, J3.09, J3.14, J3.20, J3.25, J3.30, J3.34, J3.39, U7.3 (A2), U7.4 (VSS), U7.9 (EP); also elsewhere on the board

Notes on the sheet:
Device Address configurable as 1010_A2_A1_A0 Raspberry Pi Power Hat MODE1 = 1010011, so A2=low, A1 + A0 = high Write Protect pin WP floating = writes allowed

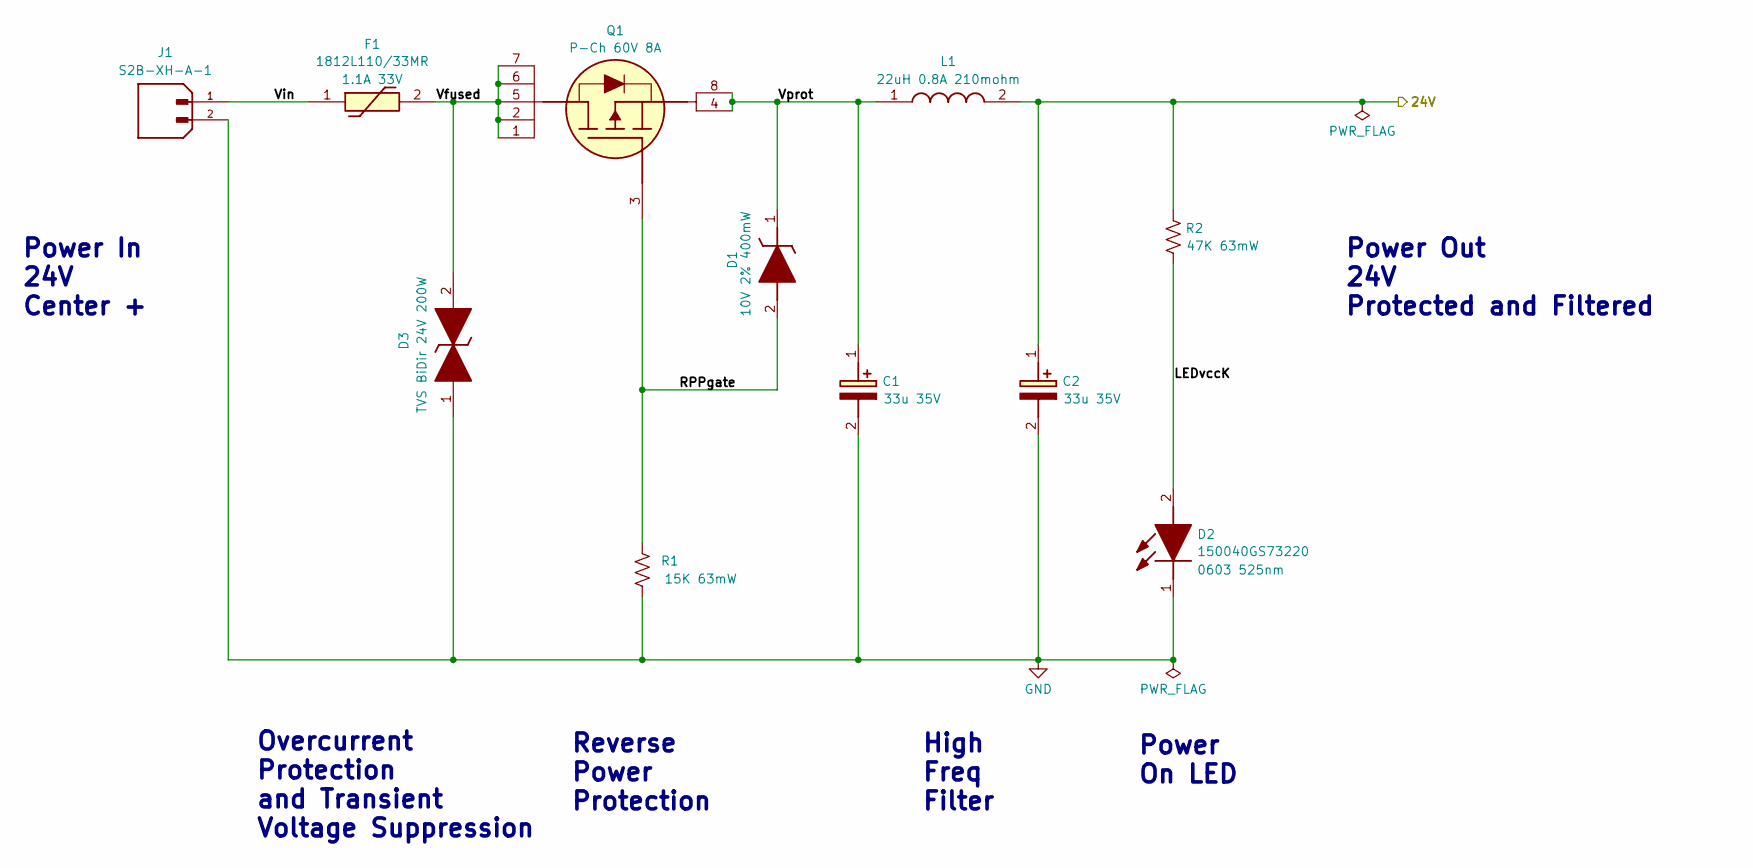
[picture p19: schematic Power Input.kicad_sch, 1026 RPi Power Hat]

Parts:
C1, C2: T521D336M035ATE065; [C] Kemet Tantalum Polymer T521X; Mouser Part Number 80-T521D336M35ATE65
D1: PDZ10B,115; [D] Nexperia Zener PDZ10B,115 10V; Mouser Part Number 771-PDZ10B115
D2: 150040GS73220; [D] Wurth Elektronik 150040GS73220; Mouser Part Number 710-150040GS73220
D3: SMF24CA; [D] Littelfuse SMF24CA 24V 200W; Manufacturer_Part_Number SMF24CA; Mouser Part Number 576-SMF24CA
F1: 1812L110/33MR; [F] Littelfuse PPTC 1812L010DR; Mouser Part Number 576-1812L110/33MR
J1: S2B-XH-A-1; [J] JST S2B-XH-A-1; Mouser Part Number 306-S2BXHA1LFSN; DigiKey_Part_Number 455-S2B-XH-A-1-ND
L1: LPS4040-223; [L] Coilcraft Inductor LPS4040; Manufacturer_Part_Number LPS4040-223
Q1: BUK6D120-60PX; [Q] Nexperia BUK6D120-60PX P-Ch 60V 8A; Manufacturer_Part_Number BUK6D120-60PX; Mouser Part Number 771-BUK6D120-60PX
R1: 15K; R_0402_1005Metric; Manufacturer_Part_Number CRCW040215K0FKED; Mouser Part Number 71-CRCW0402-15K-E3
R2: 47K; R_0402_1005Metric; Manufacturer_Part_Number CRCW040247K0FKED; Mouser Part Number 71-CRCW0402-47K-E3

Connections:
/5V Regulator/24V: C2.1 (+), L1.2, R2.1; also elsewhere on the board
/Power Input/LEDvccK: D2.2 (A), R2.2
/Power Input/RPPgate: D1.2 (A), Q1.3 (G), R1.1
/Power Input/Vfused: D3.2, F1.2, Q1.1 (D_1), Q1.2 (D_2), Q1.5 (D_3), Q1.6 (D_4), Q1.7 (D_5)
/Power Input/Vin: F1.1, J1.1
/Power Input/Vprot: C1.1 (+), D1.1 (K), L1.1, Q1.4 (S_1), Q1.8 (S_2)
GND: C1.2 (-), C2.2 (-), D2.1 (K), D3.1, J1.2, R1.2; also elsewhere on the board

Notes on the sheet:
Reverse Power Protection
Power On LED
Overcurrent Protection and Transient Voltage Suppression
High Freq Filter
Power In 24V Center +
Power Out 24V Protected and Filtered

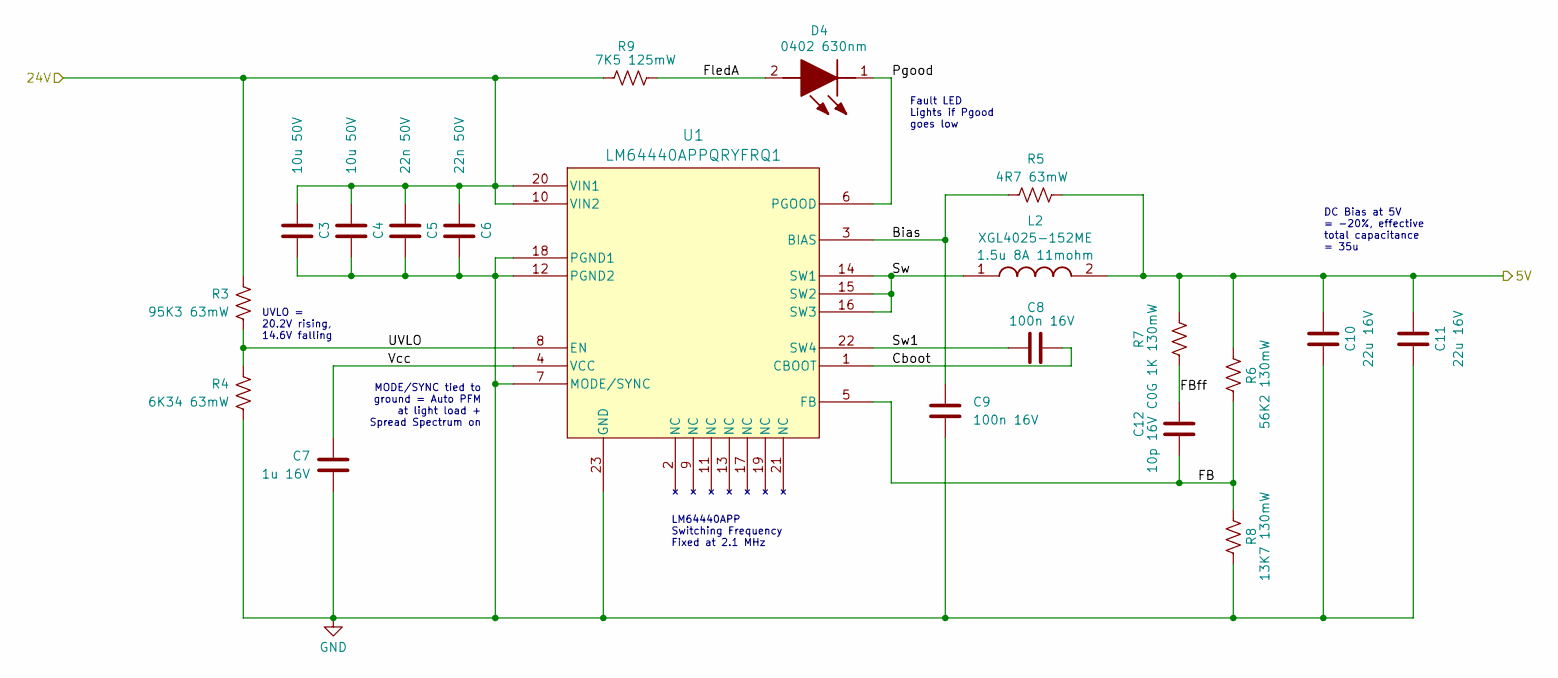
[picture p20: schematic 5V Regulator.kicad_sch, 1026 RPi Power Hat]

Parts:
C3, C4: GRJ32ER71H106KE11K; C_1210_3225Metric; Manufacturer_Part_Number GRJ32ER71H106KE11K; Mouser Part Number 81-GRJ32ER71H106KE1K
C5, C6: GCM155R71H223KA55D; C_0402_1005Metric; Manufacturer_Part_Number GCM155R71H223KA55D; Mouser Part Number 81-GCM155R71H223KA5D
C7: GCM188R71C105KA64J; C_0603_1608Metric; Manufacturer_Part_Number GCM188R71C105KA64J; Mouser Part Number 81-GCM188R71C105KA4J
C8, C9: GCM155R71C104KA55D; C_0402_1005Metric; Manufacturer_Part_Number GCM155R71C104KA55D; Mouser Part Number 81-GCM155R71C104KA5D
C10, C11: GCM32ER71C226ME19L; C_1210_3225Metric; Manufacturer_Part_Number GCM32ER71C226ME19L; Mouser Part Number 81-GCM32ER71C226ME9L
C12: VJ0402A100GXJCW1BC; C_0402_1005Metric; Manufacturer_Part_Number VJ0402A100GXJCW1BC; Mouser Part Number 77-VJ0402A100GXJCBC
D4: 150040RS73240; [D] Wurth Elektronik 150040RS73240; Mouser Part Number 710-150040RS73240
L2: XGL4025-152ME; [L] Coilcraft Inductor XGL4025; Manufacturer_Part_Number XGL4025-152ME
R3: 95K3; R_0402_1005Metric; Manufacturer_Part_Number CRCW040295K3FKED; Mouser Part Number 71-CRCW0402-95.3K-E3
R4: 6K34; R_0402_1005Metric; Manufacturer_Part_Number CRCW04026K34FKEDC; Mouser Part Number 71-CRCW04026K34FKEDC
R5: 4R7; R_0402_1005Metric; Manufacturer_Part_Number CRCW04024R70FNED; Mouser Part Number 71-CRCW04024R70FNED
R6: 56K2; R_0402_1005Metric; Manufacturer_Part_Number TNPW040256K2BEED; Mouser Part Number 71-TNPW040256K2BEED
R7: 1K; R_0402_1005Metric; Manufacturer_Part_Number TNPW04021K00BEED; Mouser Part Number 71-TNPW04021K00BEED
R8: 13K7; R_0402_1005Metric; Manufacturer_Part_Number TNPW040213K7BEED; Mouser Part Number 71-TNPW040213K7BEED
R9: 7K5; R_0402_1005Metric; Manufacturer_Part_Number RCC04027K50FKED; Mouser Part Number 71-RCC04027K50FKED
U1: LM64440APPQRYFRQ1; [U] TI LM63460 Sw Volt Reg; Manufacturer_Part_Number LM64440APPQRYFRQ1; Mouser Part Number 595-LM64440APPQRYRQ1

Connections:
/5V Regulator/5V: C10.1, C11.1, L2.2, R5.2, R6.1, R7.1; also elsewhere on the board
/5V Regulator/24V: C3.1, C4.1, C5.1, C6.1, R3.1, R9.1, U1.10 (VIN2), U1.20 (VIN1); also elsewhere on the board
/5V Regulator/Bias: C9.2, R5.1, U1.3 (BIAS)
/5V Regulator/Cboot: C8.2, U1.1 (CBOOT)
/5V Regulator/FB: C12.1, R6.2, R8.2, U1.5 (FB)
/5V Regulator/FBff: C12.2, R7.2
/5V Regulator/FledA: D4.2 (A), R9.2
/5V Regulator/Pgood: D4.1 (K), U1.6 (PGOOD)
/5V Regulator/Sw: L2.1, U1.14 (SW1), U1.15 (SW2), U1.16 (SW3)
/5V Regulator/Sw1: C8.1, U1.22 (SW4)
/5V Regulator/UVLO: R3.2, R4.1, U1.8 (EN)
/5V Regulator/Vcc: C7.1, U1.4 (VCC)
GND: C3.2, C4.2, C5.2, C6.2, C7.2, C9.1, C10.2, C11.2, R4.2, R8.1, U1.7 (MODE/SYNC), U1.12 (PGND2), U1.18 (PGND1), U1.23 (GND); also elsewhere on the board

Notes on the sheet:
MODE/SYNC tied to ground = Auto PFM at light load + Spread Spectrum on
Fault LED Lights if Pgood goes low
DC Bias at 5V = -20%, effective total capacitance = 35u
LM64440APP Switching Frequency Fixed at 2.1 MHz
UVLO = 20.2V rising, 14.6V falling

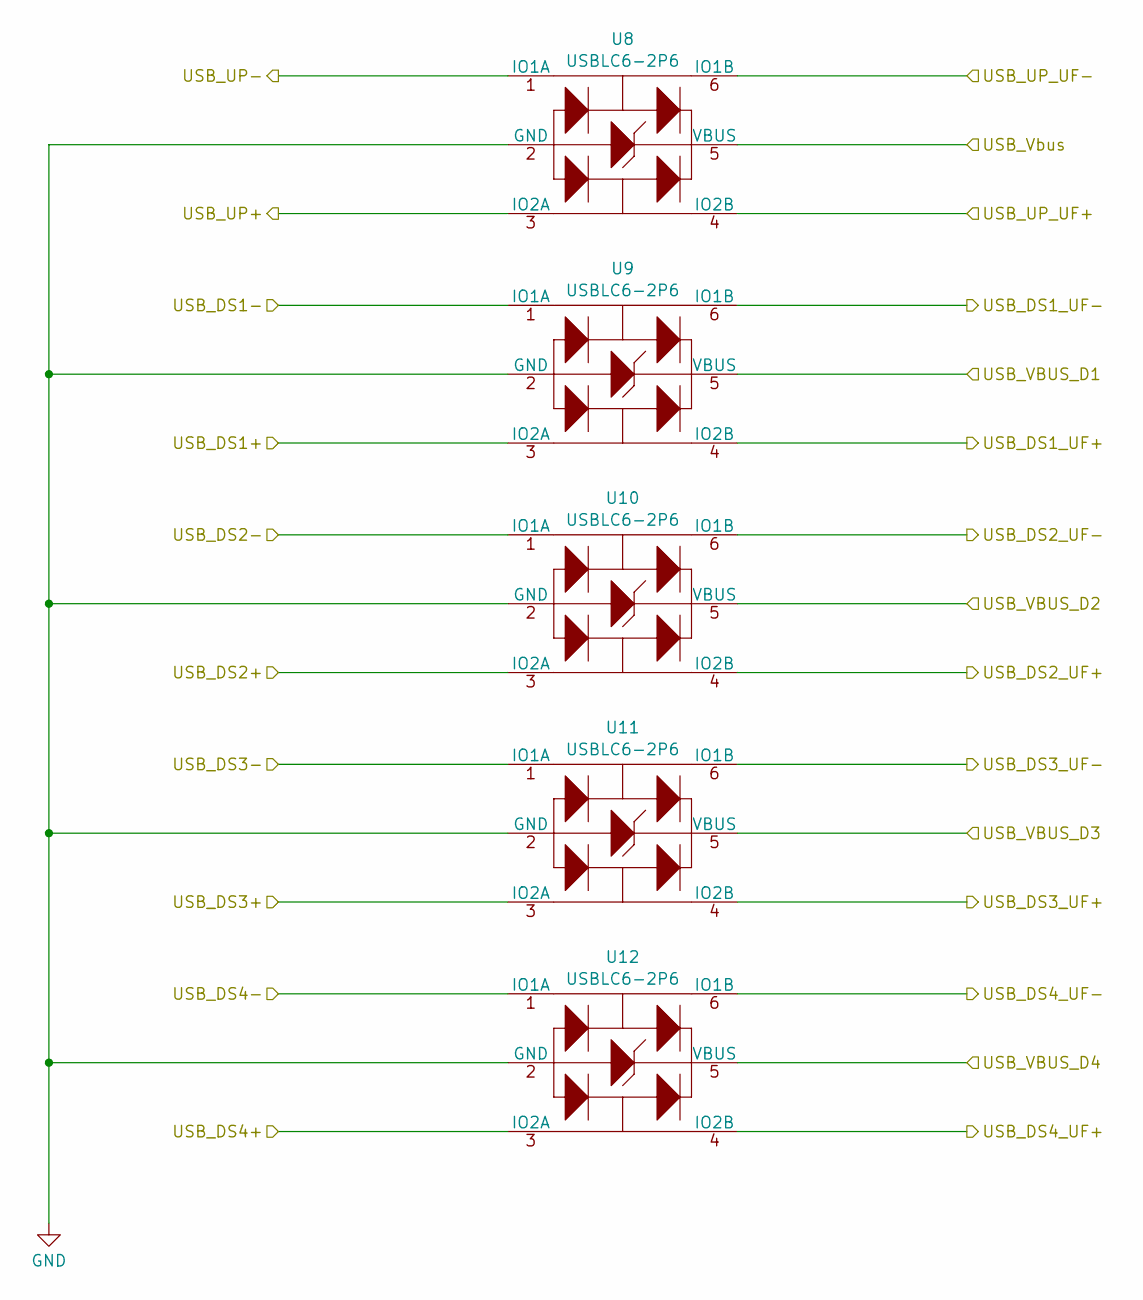
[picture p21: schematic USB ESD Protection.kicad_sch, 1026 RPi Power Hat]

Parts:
U8, U9, U10, U11, U12: USBLC6-2P6; [U] ST Micro USB ESD Protection USBLC6-2P6; Manufacturer_Part_Number USBLC6-2P6; Mouser Part Number 511-USBLC6-2P6

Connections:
/USB ESD Protection/USB_DS1_UF+: U9.4 (IO2B); also elsewhere on the board
/USB ESD Protection/USB_DS1_UF-: U9.6 (IO1B); also elsewhere on the board
/USB ESD Protection/USB_DS2_UF+: U10.4 (IO2B); also elsewhere on the board
/USB ESD Protection/USB_DS2_UF-: U10.6 (IO1B); also elsewhere on the board
/USB ESD Protection/USB_DS3_UF+: U11.4 (IO2B); also elsewhere on the board
/USB ESD Protection/USB_DS3_UF-: U11.6 (IO1B); also elsewhere on the board
/USB ESD Protection/USB_DS4_UF+: U12.4 (IO2B); also elsewhere on the board
/USB ESD Protection/USB_DS4_UF-: U12.6 (IO1B); also elsewhere on the board
/USB ESD Protection/USB_UP_UF+: U8.4 (IO2B); also elsewhere on the board
/USB ESD Protection/USB_UP_UF-: U8.6 (IO1B); also elsewhere on the board
/USB ESD Protection/USB_VBUS_D1: U9.5 (VBUS); also elsewhere on the board
/USB ESD Protection/USB_VBUS_D2: U10.5 (VBUS); also elsewhere on the board
/USB ESD Protection/USB_VBUS_D3: U11.5 (VBUS); also elsewhere on the board
/USB ESD Protection/USB_VBUS_D4: U12.5 (VBUS); also elsewhere on the board
/USB Hub/USB_DS1+: U9.3 (IO2A); also elsewhere on the board
/USB Hub/USB_DS1-: U9.1 (IO1A); also elsewhere on the board
/USB Hub/USB_DS2+: U10.3 (IO2A); also elsewhere on the board
/USB Hub/USB_DS2-: U10.1 (IO1A); also elsewhere on the board
/USB Hub/USB_DS3+: U11.3 (IO2A); also elsewhere on the board
/USB Hub/USB_DS3-: U11.1 (IO1A); also elsewhere on the board
/USB Hub/USB_DS4+: U12.3 (IO2A); also elsewhere on the board
/USB Hub/USB_DS4-: U12.1 (IO1A); also elsewhere on the board
/USB Hub/USB_UP+: U8.3 (IO2A); also elsewhere on the board
/USB Hub/USB_UP-: U8.1 (IO1A); also elsewhere on the board
/USB Hub/USB_Vbus: U8.5 (VBUS); also elsewhere on the board
GND: U8.2 (GND), U9.2 (GND), U10.2 (GND), U11.2 (GND), U12.2 (GND); also elsewhere on the board

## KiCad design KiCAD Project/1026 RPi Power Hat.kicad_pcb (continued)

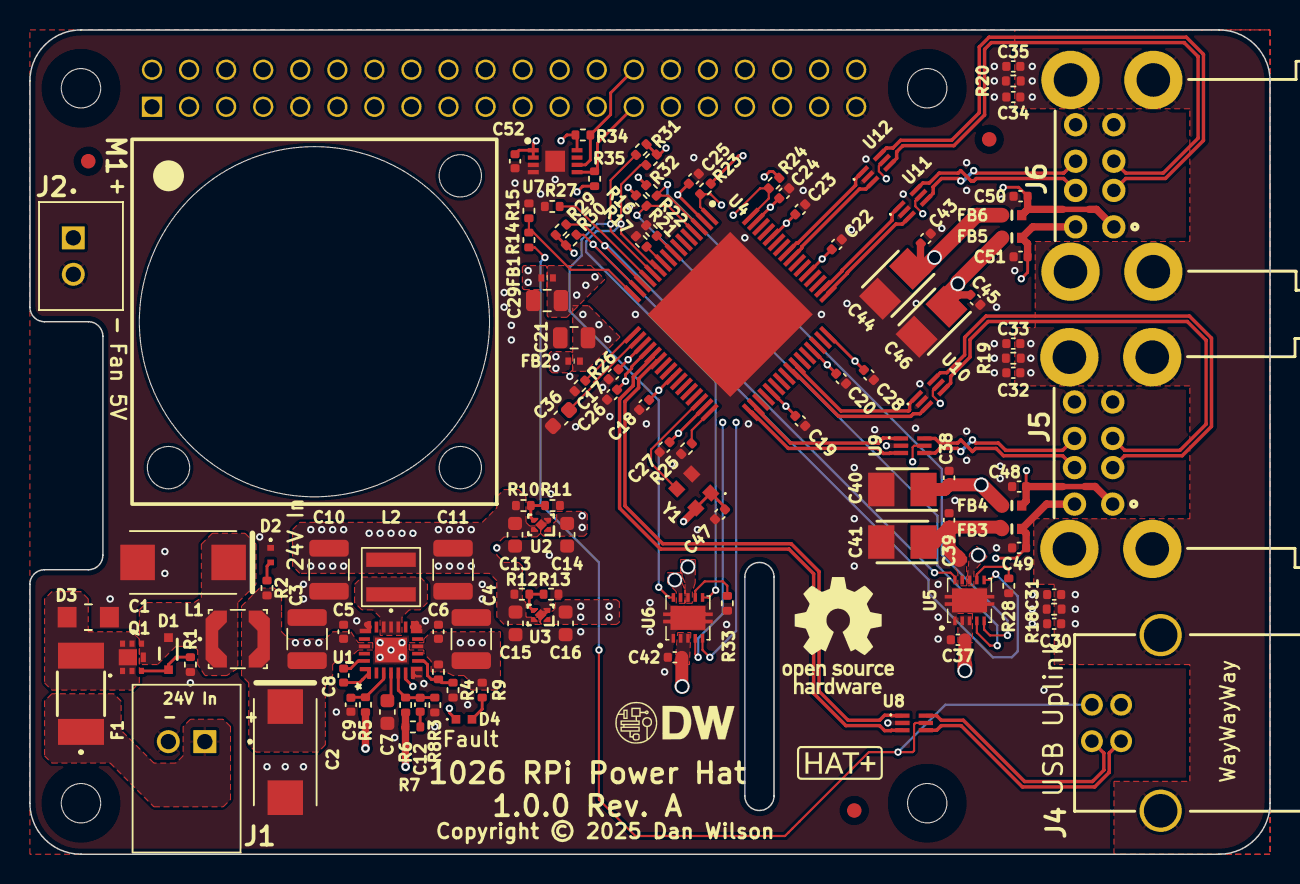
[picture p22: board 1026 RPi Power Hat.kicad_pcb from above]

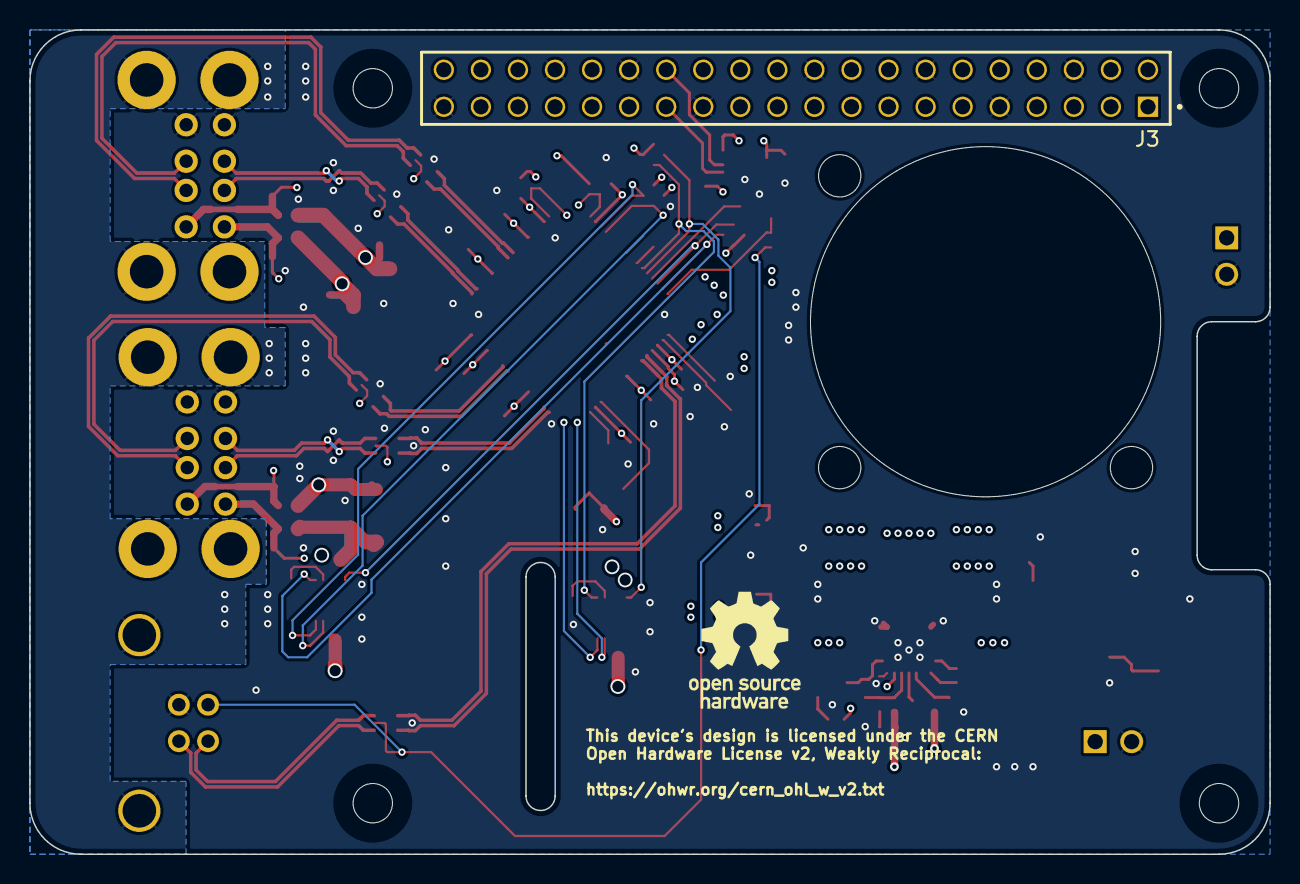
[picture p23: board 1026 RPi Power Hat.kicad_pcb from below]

Board: 4 copper layers, 85.0 x 56.5 mm, 132 parts (2 on the bottom side), 74 nets.

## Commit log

2025-04-21 v1.0.0 RC
    v1.0.0 of 1026 Raspberry Pi Power HAT, candidate for initial production.
    [1026 RPi Power Hat-B_Cu.gbr, 1026 RPi Power Hat-B_Mask.gbr, 1026 RPi Power Hat-B_Paste.gbr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]
2025-04-21 v1.0.0 RC2
    Build candidate 2
    [1026 RPi Power Hat-B_Cu.gbr, 1026 RPi Power Hat-B_Mask.gbr, 1026 RPi Power Hat-B_Paste.gbr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]
2025-05-03 v1.0.0 RC3
    Minor change to upstream USB port to connect Vbus to ESD protection vice on-board 5V.
    [1026 Air Pick Assembly.xlsm, 1026 RPi Power Hat.csv, 1026 RPi Power Hat.kicad_pcb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]
2025-05-18 v1.0.0
    Initial Commit
    [1026 RPi Power Hat-B_Cu.gbr, 1026 RPi Power Hat-B_Mask.gbr, 1026 RPi Power Hat-B_Paste.gbr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]
2025-07-06 v1.0.0A
    Moved all symbols, footprints, and 3D models to local project-specific libraries in /KiCAD Project/Libraries.
    [1026 RPi Power Hat.kicad_pcb, 5V Regulator.kicad_sch, Fan Header and Fan.kicad_sch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]
2025-07-09 Update .gitignore
    Update .gitignore file to exclude KiCAD auto-backups and lock files.
2025-07-22 Solder mask, parts and text updates
    Use pass through header ESW-120-34-G-D vs ESW-120-33-G-D
    Add PCBWay test WayWayWay under J4
    Change board name text to be "1026 RPi Power Hat"
    Add board version text "1.0.0 Rev A"
    Change Solder Mask clearance from 0 to -0.01 on U4 in footprint properties for PCBway minimum clearance of 0.22mm
    Change board silkscreen color to Black
    Remove references to unused Jua font
    [1026 RPi Power Hat.kicad_pcb]
2025-07-22 New BOM for new Parts
    Add ESW-120-34-G-D and remove ESW-120-33-G-D. Update BOM and iBOM.
    [1026 RPi Power Hat.csv, 1026 RPi Power Hat.kicad_pcb, Fan Header and Fan.kicad_sch]
2025-07-26 Prep for PCBway
    Verified all parts reference local libraries, update font for PCB board title to Noto Sans font, add Noto Sans fonts to project folder, update 3D image for documentation, update documentation for lin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
    [1026 RPi Power Hat-B_Cu.gbr, 1026 RPi Power Hat-B_Mask.gbr, 1026 RPi Power Hat-B_Paste.gbr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]

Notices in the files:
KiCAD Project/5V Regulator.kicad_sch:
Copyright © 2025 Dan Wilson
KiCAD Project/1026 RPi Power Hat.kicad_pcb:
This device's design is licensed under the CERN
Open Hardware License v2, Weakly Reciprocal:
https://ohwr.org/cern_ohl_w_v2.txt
